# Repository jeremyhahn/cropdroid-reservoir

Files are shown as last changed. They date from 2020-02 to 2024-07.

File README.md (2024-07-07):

# cropdroid-reservoir

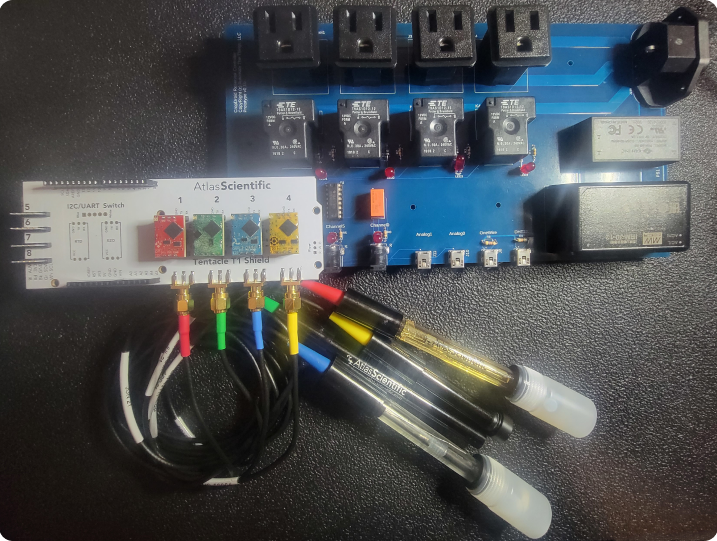
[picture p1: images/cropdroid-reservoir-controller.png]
[](https://github.com/jeremyhahn/cropdroid-reservoir)

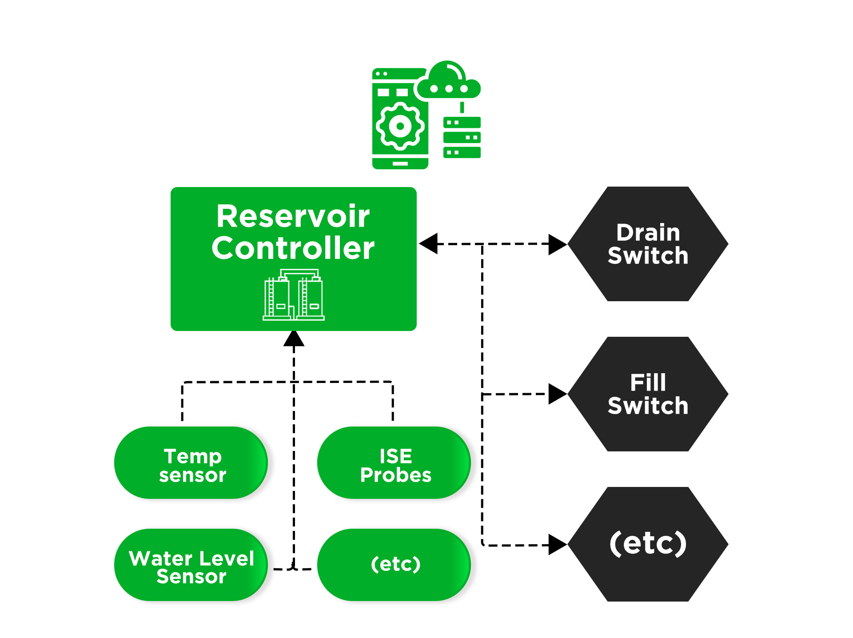
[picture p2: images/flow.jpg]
[](https://github.com/jeremyhahn/cropdroid-reservoir)

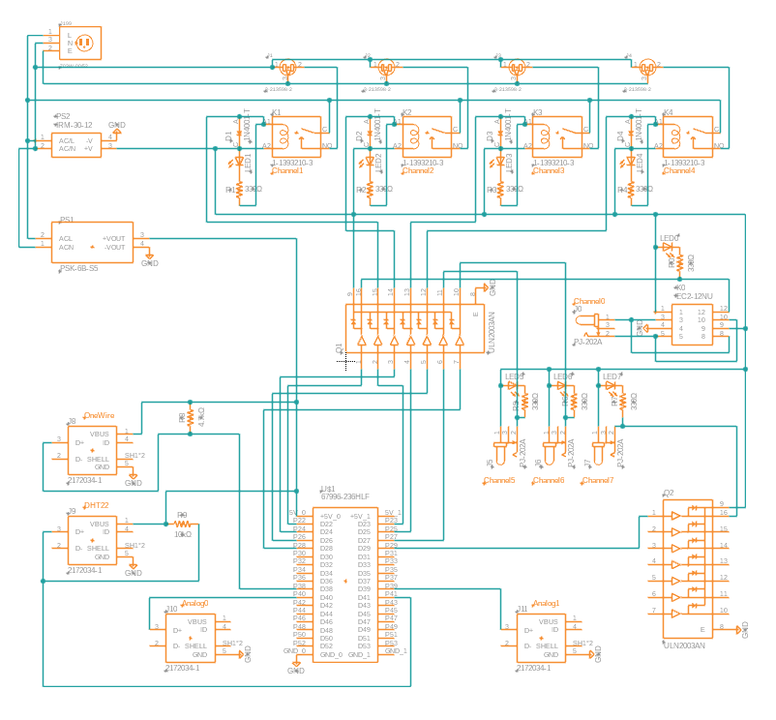
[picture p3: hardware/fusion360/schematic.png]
[](https://github.com/jeremyhahn/cropdroid-reservoir/blob/master/hardware/fusion360/schematic.png)

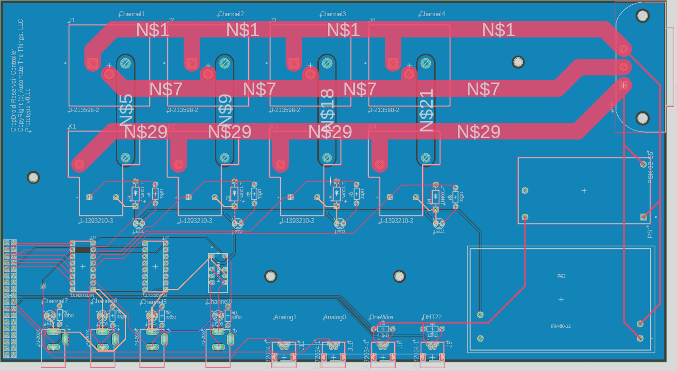
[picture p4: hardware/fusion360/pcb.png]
[](https://github.com/jeremyhahn/cropdroid-reservoir/blob/master/hardware/fusion360/pcb.png)

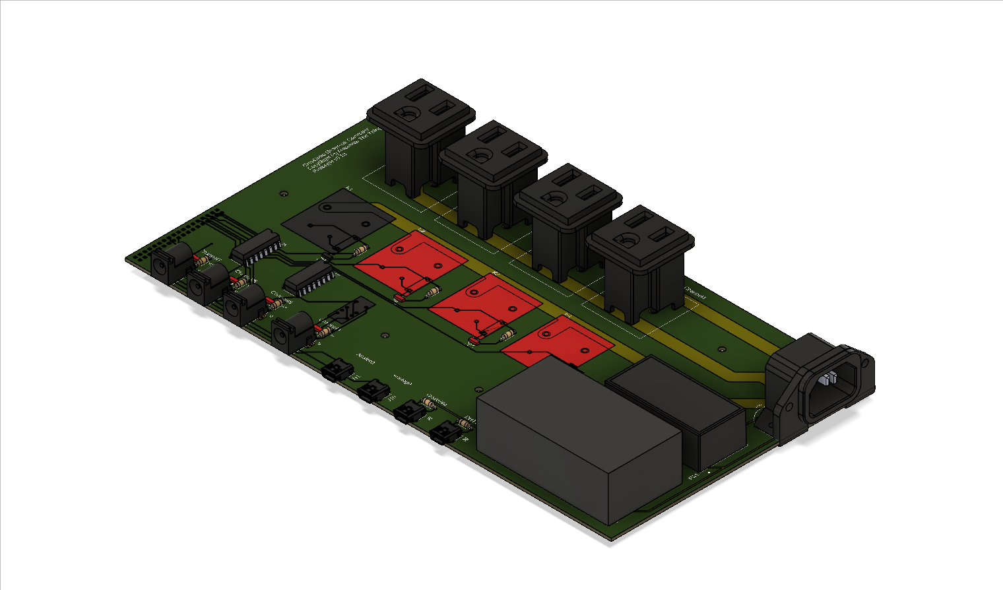
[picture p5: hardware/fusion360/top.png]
[](https://github.com/jeremyhahn/cropdroid-reservoir/blob/master/hardware/fusion360/top.png)

[](https://github.com/jeremyhahn/cropdroid-reservoir/blob/master/hardware/fusion360/top2.png)

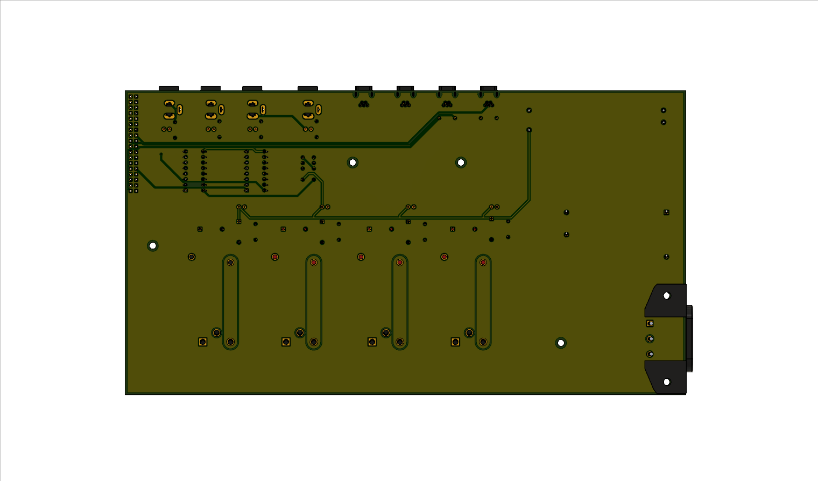
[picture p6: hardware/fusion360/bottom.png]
[](https://github.com/jeremyhahn/cropdroid-reservoir/blob/master/hardware/fusion360/bottom.png)

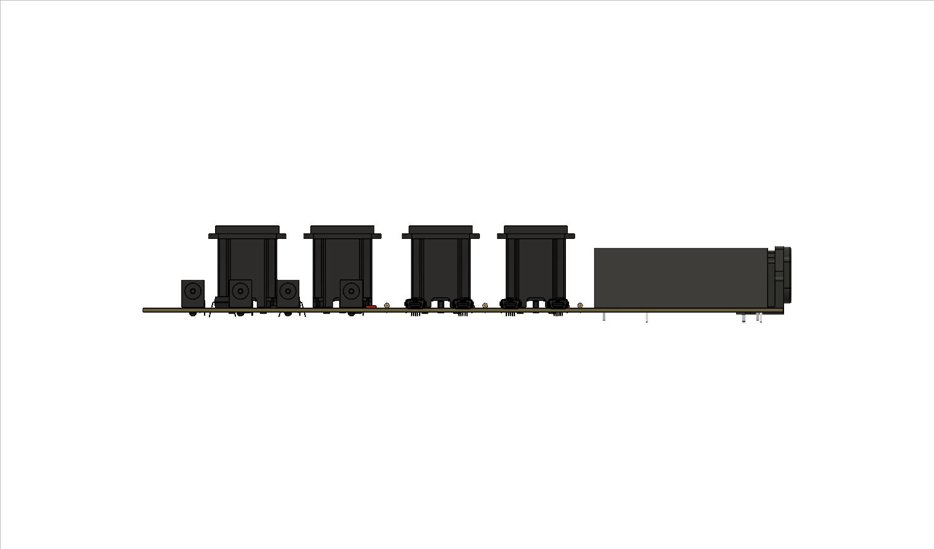
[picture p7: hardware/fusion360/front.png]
[](https://github.com/jeremyhahn/cropdroid-reservoir/blob/master/hardware/fusion360/front.png)

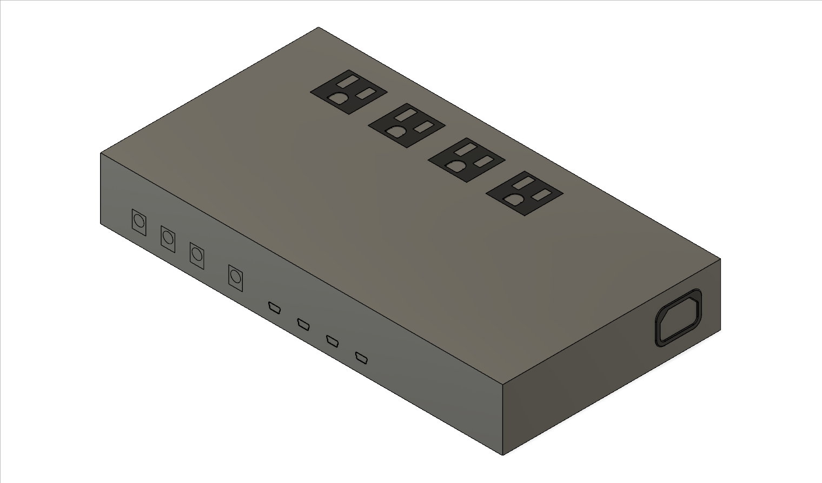
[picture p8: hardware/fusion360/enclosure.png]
[](https://github.com/jeremyhahn/cropdroid-reservoir/blob/master/hardware/fusion360/enclosure.png)

## Support

Please consider supporting this project for ongoing success and sustainability. I'm a passionate open source contributor making a professional living creating free, secure, scalable, robust, enterprise grade, distributed systems and cloud native solutions.

I'm also available for international consulting opportunities. Please let me know how I can assist you or your organization in achieving your desired security posture and technology goals.

https://github.com/sponsors/jeremyhahn

https://www.linkedin.com/in/jeremyhahn

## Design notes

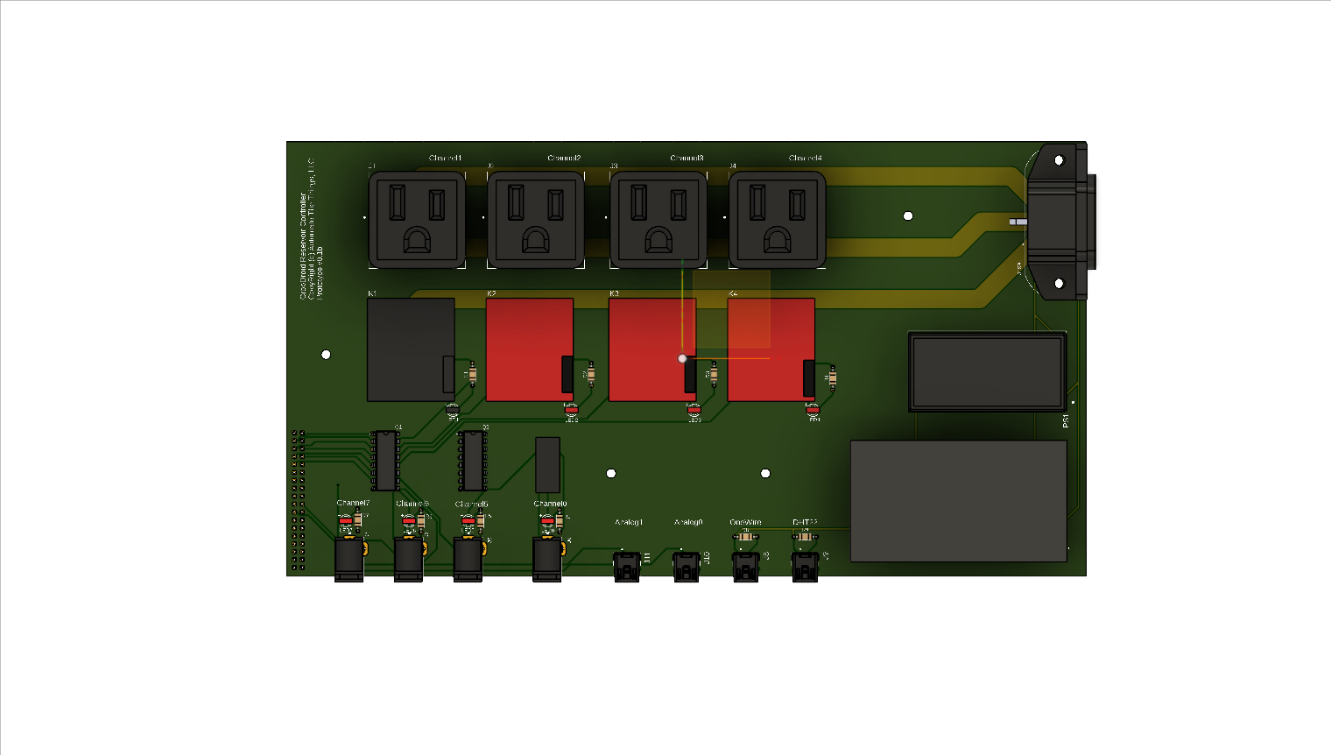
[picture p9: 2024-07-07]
hardware/fusion360/top-2.png

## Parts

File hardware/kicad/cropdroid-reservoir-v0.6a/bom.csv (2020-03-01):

Reference | Quantity | Value | Footprint | Datasheet | Category | DK_Datasheet_Link | DK_Detail_Page | Description | Digi-Key_PN | Family | MPN | Manufacturer | Status | Field4 | Field5 | Field6
D2 D4 D6 D8 | 4 | LED | libraries:CAPPRD350W60D800H2000 | ~
D3 D1 D5 D7 | 4 | 1N4001 | Diode_THT:D_DO-41_SOD81_P10.16mm_Horizontal | http://www.vishay.com/docs/88503/1n4001.pdf
J1 | 1 | 703W-00_52 | 703W-00_52:QUALTEK_703W-00_52 | B |  |  |  |  |  |  |  |  |  | Manufacturer Recommendations | Qualtek
J11 J12 J13 J14 J4 J10 | 6 | PJ-102A | digikey-footprints:Barrel_Jack_5.5mmODx2.1mmID_PJ-102A | https://www.cui.com/product/resource/digikeypdf/pj-102a.pdf | Connectors, Interconnects | https://www.cui.com/product/resource/digikeypdf/pj-102a.pdf | /product-detail/en/cui-inc/PJ-102A/CP-102A-ND/275425 | CONN PWR JACK 2X5.5MM SOLDER | CP-102A-ND | Barrel - Power Connectors | PJ-102A | CUI Inc. | Active
J3 J2 | 2 | 2172034-1 | TE_2172034-1 | Compliant |  |  |  |  |  |  |  |  |  | 2172034-1 | https://www.te.com/usa-en/product-2172034-1.html?te_bu=Cor&te_type=disp&elqCampaignId=32493
J6 J8 J5 J9 | 4 | 3-213598-2 | 3-213598-2:TE_3-213598-2 | https://www.te.com/usa-en/product-3-213598-2.html?te_bu=Cor&te_type=disp&elqCampaignId=32493 |  |  |  |  |  |  |  |  |  | Compliant | 3-213598-2 | Convenience Outlet
J7 | 1 | SAMTEC-MTSW-118-10-X-D-640 | SAMTEC-MTSW-118-10-X-D-640:SAMTEC-MTSW-118-10-X-D-640
K1 K2 K3 K4 | 4 | T9AS1D12-15 | T9AS1D12-15:RELAY_T9AS1D12-15 | https://www.te.com/usa-en/product-1-1393210-4.html?te_bu=Cor&te_type=disp&elqCampaignId=32493 |  |  |  |  |  |  |  |  |  | 1-1393210-4
PS1 | 1 | PSK-6B-S5 | PSK-6B-S5:CONV_PSK-6B-S5 | CUI Inc |  |  |  |  |  |  |  |  |  | Manufacturer recommendations | 1.0
Q1 Q2 | 2 | ULN2003AN | digikey-footprints:DIP-16_W7.62mm | http://www.ti.com/general/docs/suppproductinfo.tsp?distId=10 | Discrete Semiconductor Products | http://www.ti.com/general/docs/suppproductinfo.tsp?distId=10 | /product-detail/en/texas-instruments/ULN2003AN/296-1979-5-ND/277624 | IC PWR RELAY 7NPN 1:1 16DIP | 296-1979-5-ND | Transistors - Bipolar (BJT) - Arrays | ULN2003AN | Texas Instruments | Active
R1 | 1 | 10k | Resistor_THT:R_Axial_DIN0207_L6.3mm_D2.5mm_P10.16mm_Horizontal | ~
R2 | 1 | 4.7k | Resistor_THT:R_Axial_DIN0207_L6.3mm_D2.5mm_P10.16mm_Horizontal | ~
R3 R4 R5 R6 | 4 | R | Resistor_THT:R_Axial_DIN0207_L6.3mm_D2.5mm_P10.16mm_Horizontal | ~
RLY1 | 1 | EC2-12NU | digikey-footprints:Relay_THT_EC2 | https://api.kemet.com/component-edge/download/datasheet/EC2-12NU.pdf | Relays | https://api.kemet.com/component-edge/download/datasheet/EC2-12NU.pdf | /product-detail/en/kemet/EC2-12NU/399-11029-5-ND/4291095 | RELAY GEN PURPOSE DPDT 2A 12VDC | 399-11029-5-ND | Signal Relays, Up to 2 Amps | EC2-12NU | KEMET | Active
U1 | 1 | IRM-30-12 | IRM-30-12:IRM-30-12

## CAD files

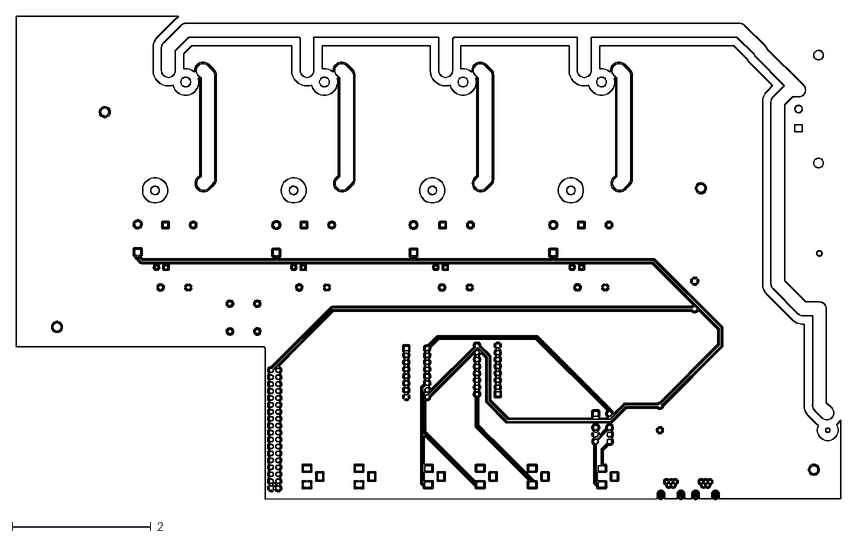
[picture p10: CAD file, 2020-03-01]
hardware/kicad/cropdroid-reservoir-v0.6a/gerber/cropdroid-reservoir-v0.6a-dxf/cropdroid-reservoir-B_Cu.dxf
11.9 x 6.97

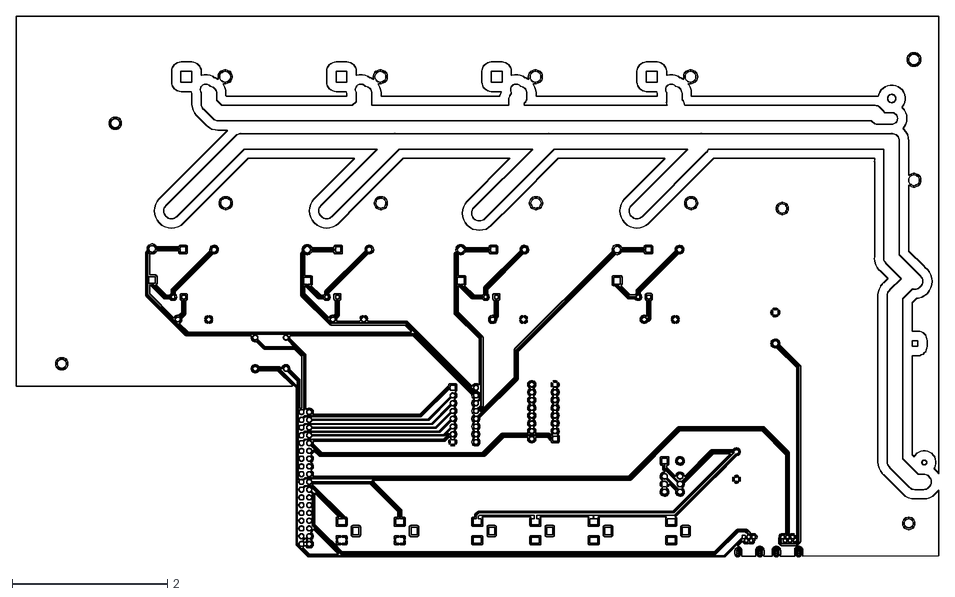
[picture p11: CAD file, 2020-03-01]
hardware/kicad/cropdroid-reservoir-v0.6a/gerber/cropdroid-reservoir-v0.6a-dxf/cropdroid-reservoir-F_Cu.dxf
11.9 x 6.97

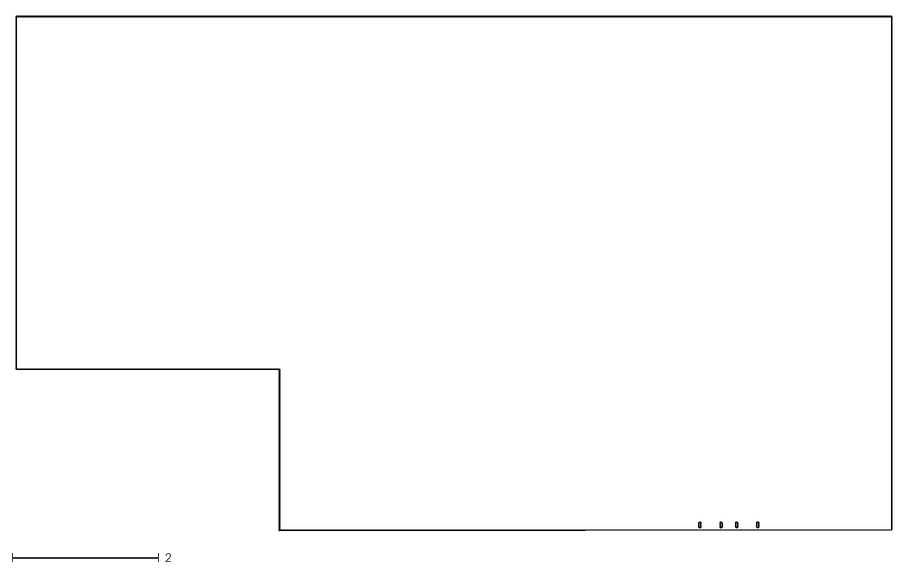
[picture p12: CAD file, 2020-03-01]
hardware/kicad/cropdroid-reservoir-v0.6a/gerber/cropdroid-reservoir-v0.6a-dxf/cropdroid-reservoir-Edge_Cuts.dxf
11.9 x 7.01

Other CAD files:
hardware/kicad/cropdroid-reservoir-v0.6a/gerber/cropdroid-reservoir-v0.6a-dxf/cropdroid-reservoir-B_Mask.dxf
hardware/kicad/cropdroid-reservoir-v0.6a/gerber/cropdroid-reservoir-v0.6a-dxf/cropdroid-reservoir-B_Paste.dxf
hardware/kicad/cropdroid-reservoir-v0.6a/gerber/cropdroid-reservoir-v0.6a-dxf/cropdroid-reservoir-F_Mask.dxf
hardware/kicad/cropdroid-reservoir-v0.6a/gerber/cropdroid-reservoir-v0.6a-dxf/cropdroid-reservoir-F_Paste.dxf
hardware/kicad/cropdroid-reservoir-v0.6a/gerber/cropdroid-reservoir-v0.6a-dxf/cropdroid-reservoir-F_SilkS.dxf

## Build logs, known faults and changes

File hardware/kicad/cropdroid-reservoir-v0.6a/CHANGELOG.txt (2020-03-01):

v0.5a
- Swap wires between pins 1 and 2 (channel 4, 5, 6)
- Change board height to accomodate vertical facing receptacles

v0.6a
- Fix upside down IRM-30-12 footprint
- Flip LED footprints
- Replace audio jacks with dc power and usb jacks
- Shorten board length

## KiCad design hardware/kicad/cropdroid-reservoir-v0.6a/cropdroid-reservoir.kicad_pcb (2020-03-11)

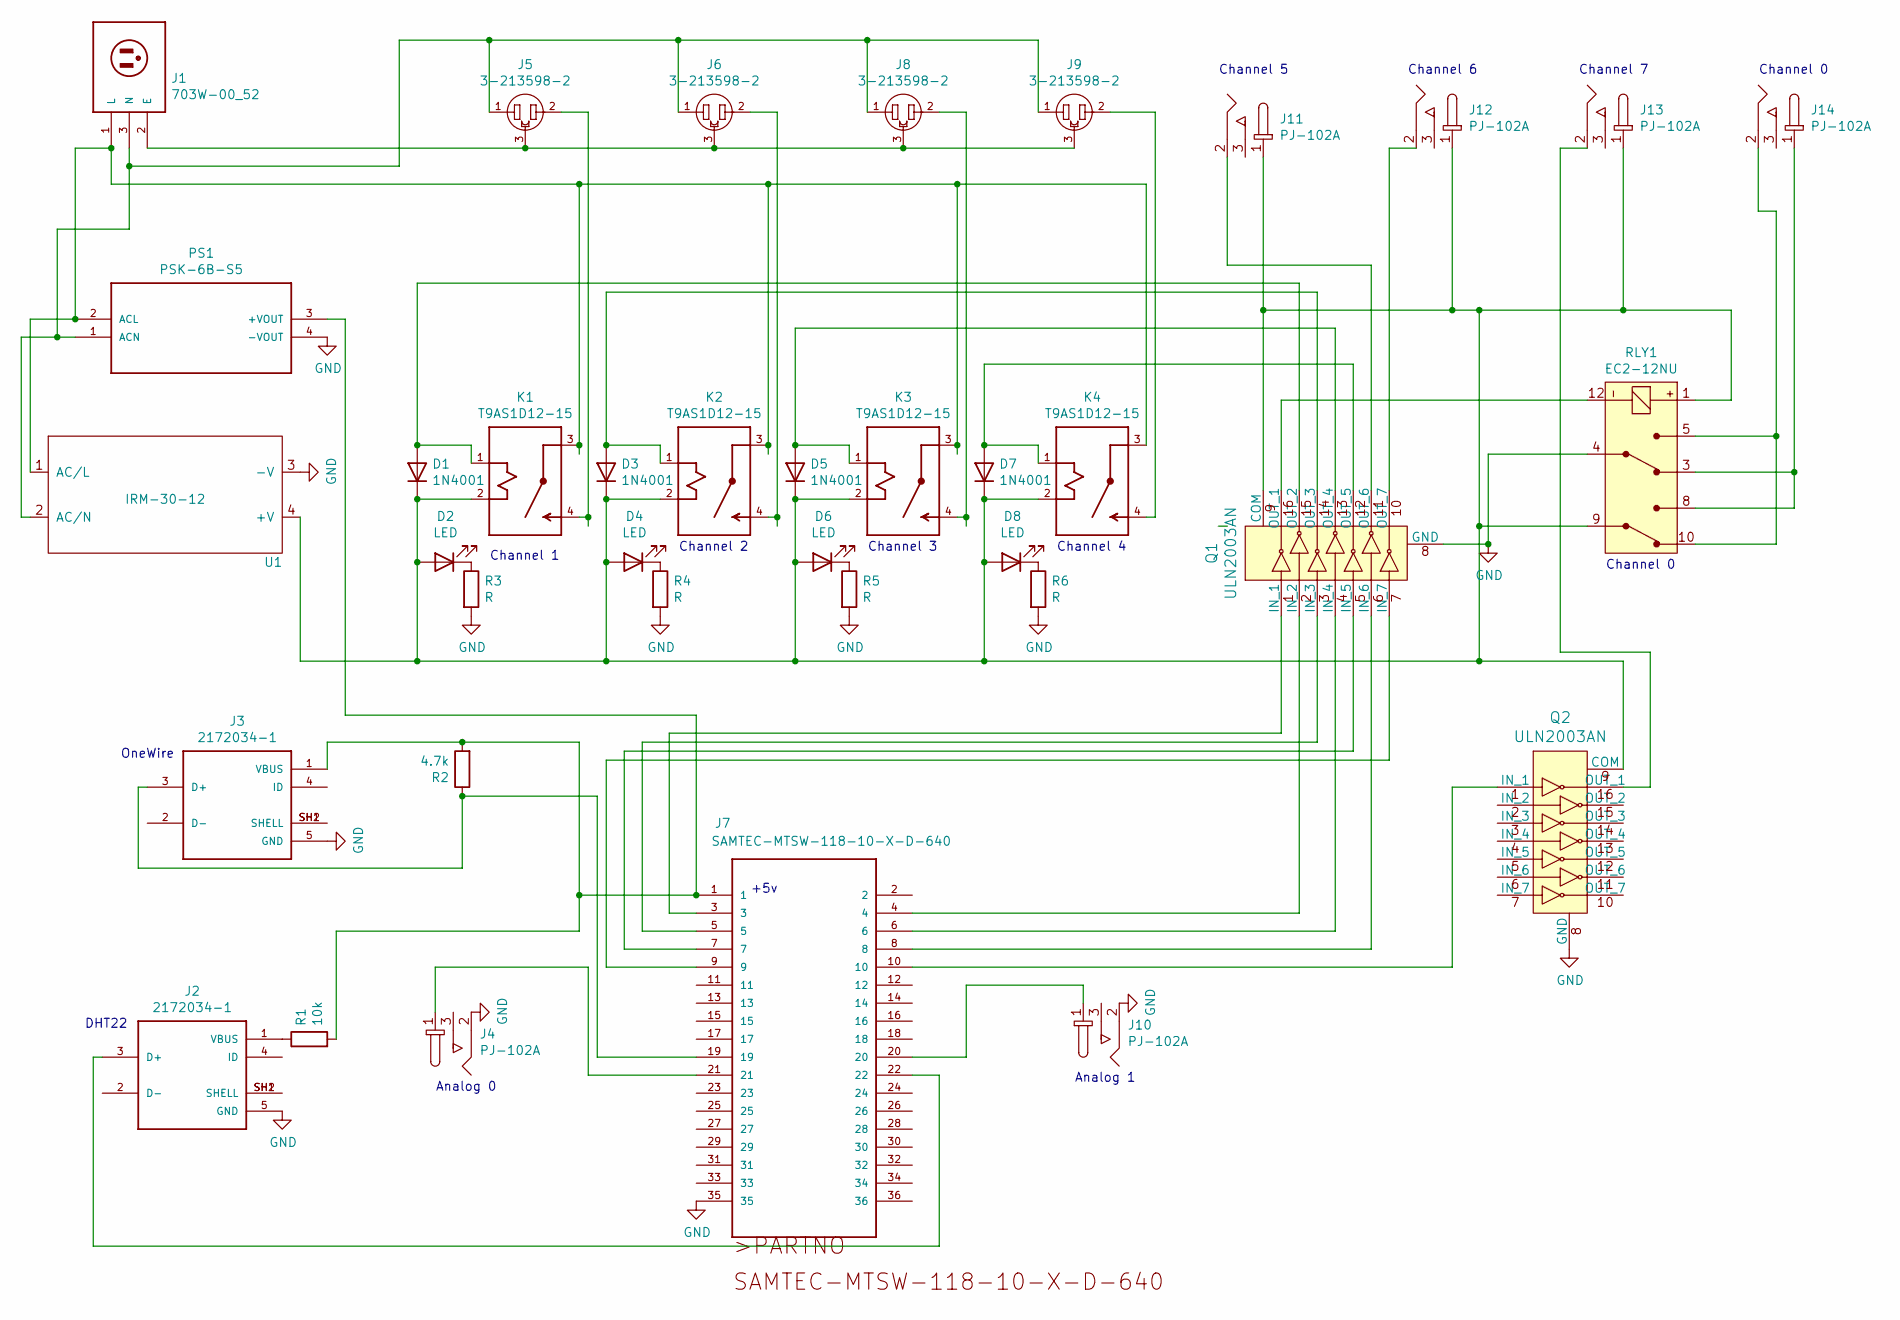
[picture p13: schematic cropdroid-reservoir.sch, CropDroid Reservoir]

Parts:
D1, D3, D5, D7: 1N4001; D_DO-41_SOD81_P10.16mm_Horizontal
D2, D4, D6, D8: LED; CAPPRD350W60D800H2000
J1: 703W-00_52; QUALTEK_703W-00_52
J2, J3: 2172034-1; TE_2172034-1
J4, J10, J11, J12, J13, J14: PJ-102A; Barrel_Jack_5.5mmODx2.1mmID_PJ-102A; MPN PJ-102A; Digi-Key_PN CP-102A-ND
J5, J6, J8, J9: 3-213598-2; TE_3-213598-2
J7: SAMTEC-MTSW-118-10-X-D-640
K1, K2, K3, K4: T9AS1D12-15; RELAY_T9AS1D12-15
PS1: PSK-6B-S5; CONV_PSK-6B-S5
Q1, Q2: ULN2003AN; DIP-16_W7.62mm; MPN ULN2003AN; Digi-Key_PN 296-1979-5-ND
R1: 10k; R_Axial_DIN0207_L6.3mm_D2.5mm_P10.16mm_Horizontal
R2: 4.7k; R_Axial_DIN0207_L6.3mm_D2.5mm_P10.16mm_Horizontal
R3, R4, R5, R6: R; R_Axial_DIN0207_L6.3mm_D2.5mm_P10.16mm_Horizontal
RLY1: EC2-12NU; Relay_THT_EC2; MPN EC2-12NU; Digi-Key_PN 399-11029-5-ND
U1: IRM-30-12

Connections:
GND: J2.5 (GND), J3.5 (GND), J4.2, J7.35, J10.2, PS1.4 (-VOUT), Q1.8 (GND), Q2.8 (GND), R3.2, R4.2, R5.2, R6.2, RLY1.4 (COM1), U1.3 (-V)
unnamed: D1.1 (K), D2.2 (A), D3.1 (K), D4.2 (A), D5.1 (K), D6.2 (A), D7.1 (K), D8.2 (A), J11.1, J12.1, J13.1, K1.2 (A2), K2.2 (A2), K3.2 (A2), K4.2 (A2), Q1.9 (COM), Q2.9 (COM), RLY1.1 (COIL), RLY1.9 (COM2), U1.4 (+V)
unnamed: D1.2 (A), K1.1 (A1), Q1.15 (OUT_2)
unnamed: D2.1 (K), R3.1
unnamed: D3.2 (A), K2.1 (A1), Q1.14 (OUT_3)
unnamed: D4.1 (K), R4.1
unnamed: D5.2 (A), K3.1 (A1), Q1.13 (OUT_4)
unnamed: D6.1 (K), R5.1
unnamed: D7.2 (A), K4.1 (A1), Q1.12 (OUT_5)
unnamed: D8.1 (K), R6.1
unnamed: J1.1 (L), K1.3 (C), K2.3 (C), K3.3 (C), K4.3 (C), PS1.2 (ACL), U1.1 (AC/L)
unnamed: J1.2 (E), J5.3, J6.3, J8.3, J9.3
unnamed: J1.3 (N), J5.1, J6.1, J8.1, J9.1, PS1.1 (ACN), U1.2 (AC/N)
unnamed: J2.1 (VBUS), R1.1
unnamed: J2.3 (D+), J7.22
unnamed: J2.SH1 (SHELL), J2.SH2 (SHELL)
unnamed: J3.1 (VBUS), J7.1, PS1.3 (+VOUT), R1.2, R2.2
unnamed: J3.3 (D+), J7.19, R2.1
unnamed: J3.SH1 (SHELL), J3.SH2 (SHELL)
unnamed: J4.1, J7.21
unnamed: J5.2, K1.4 (NO)
unnamed: J6.2, K2.4 (NO)
unnamed: J7.3, Q1.1 (IN_1)
unnamed: J7.4, Q1.2 (IN_2)
unnamed: J7.5, Q1.3 (IN_3)
unnamed: J7.6, Q1.4 (IN_4)
unnamed: J7.7, Q1.5 (IN_5)
unnamed: J7.8, Q1.6 (IN_6)
unnamed: J7.9, Q1.7 (IN_7)
unnamed: J7.10, Q2.1 (IN_1)
unnamed: J8.2, K3.4 (NO)
unnamed: J9.2, K4.4 (NO)
unnamed: J7.20, J10.1
unnamed: J11.2, Q1.11 (OUT_6)
unnamed: J12.2, Q1.10 (OUT_7)
unnamed: J13.2, Q2.16 (OUT_1)
unnamed: J14.1, RLY1.3 (NC1), RLY1.8 (NO2)
unnamed: J14.2, RLY1.5 (NO1), RLY1.10 (NC2)
unnamed: Q1.16 (OUT_1), RLY1.12 (COIL)

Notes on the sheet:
Channel 1
Channel 2
Channel 3
Channel 0
Channel 5
Channel 6
Channel 7
Analog 0
Analog 1
DHT22
+5v
Channel 4
OneWire

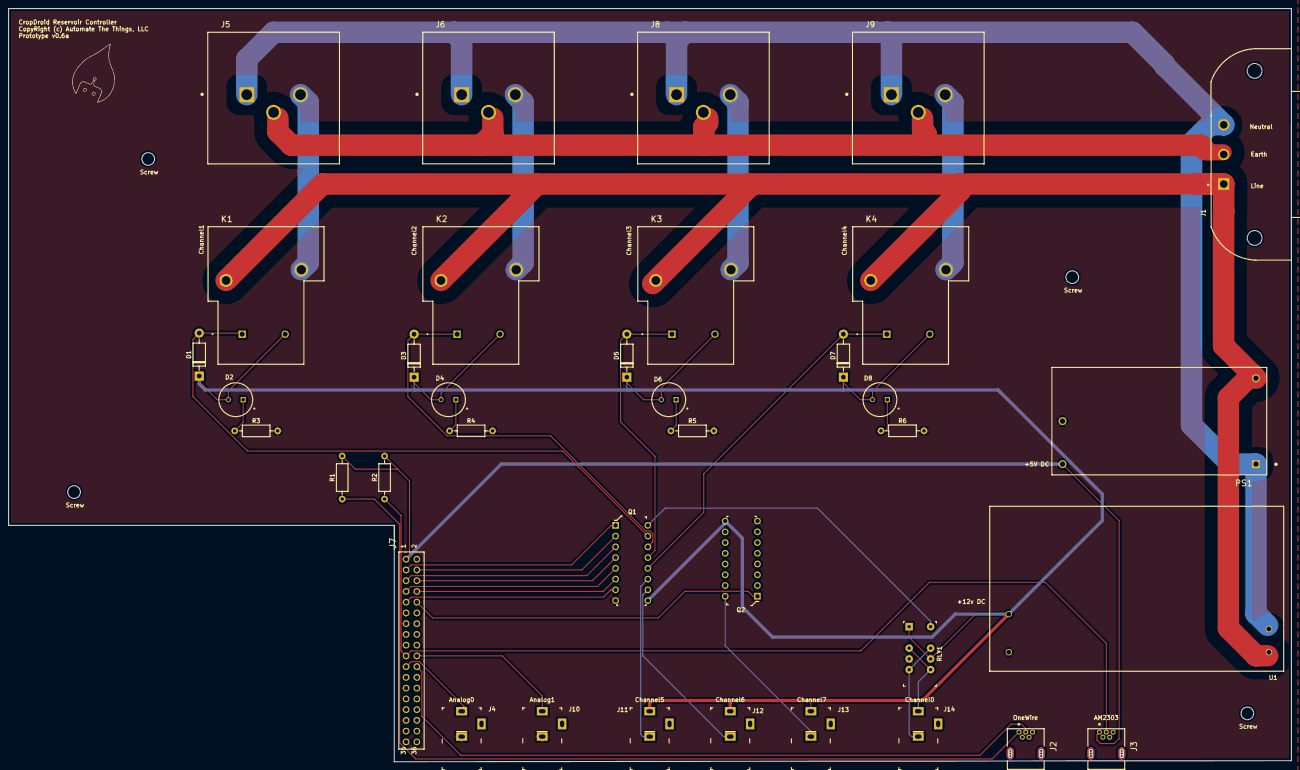
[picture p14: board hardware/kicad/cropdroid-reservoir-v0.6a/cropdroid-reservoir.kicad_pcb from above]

Board: 2 copper layers, 303.3 x 178.1 mm, 41 parts (0 on the bottom side), 39 nets.

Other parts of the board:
Screw: Drill; Drill_Hole
Screw#2, Screw#3, Screw#4: Drill; Drill_Hole

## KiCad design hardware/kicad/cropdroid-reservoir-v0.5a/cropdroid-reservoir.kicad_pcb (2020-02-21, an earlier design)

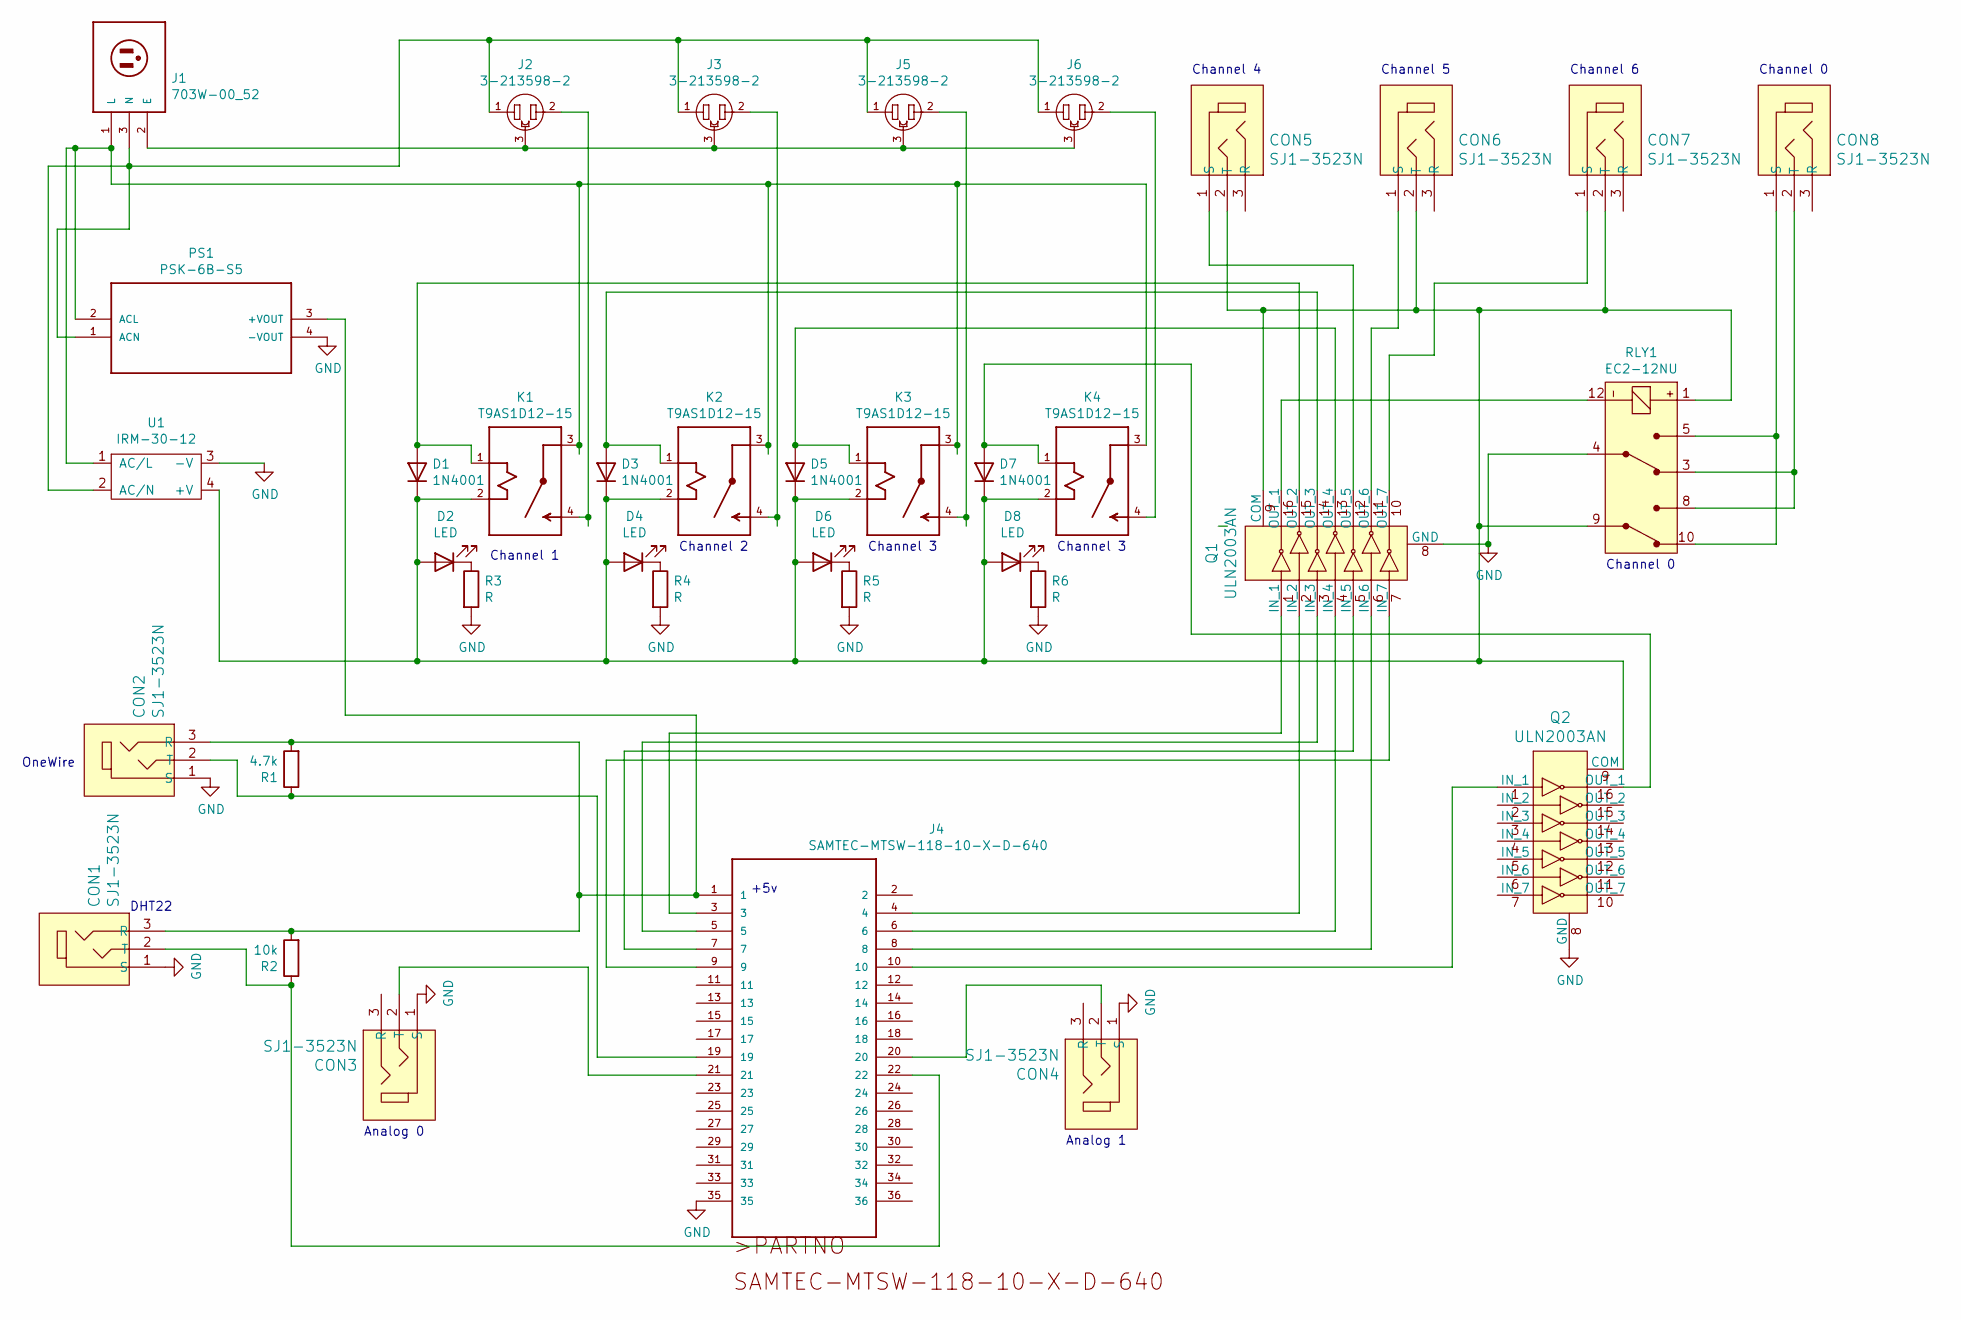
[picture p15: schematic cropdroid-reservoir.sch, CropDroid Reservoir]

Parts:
CON1, CON2, CON3, CON4, CON5, CON6, CON7, CON8: SJ1-3523N; Headphone_Jack_3.5mm_SJ1-3523N; MPN SJ1-3523N; Digi-Key_PN CP1-3523N-ND
D1, D3, D5, D7: 1N4001; D_DO-41_SOD81_P10.16mm_Horizontal
D2, D4, D6, D8: LED; CAPPRD350W60D800H2000
J1: 703W-00_52; QUALTEK_703W-00_52
J2, J3, J5, J6: 3-213598-2; TE_3-213598-2
J4: SAMTEC-MTSW-118-10-X-D-640
K1, K2, K3, K4: T9AS1D12-15; RELAY_T9AS1D12-15
PS1: PSK-6B-S5; CONV_PSK-6B-S5
Q1, Q2: ULN2003AN; DIP-16_W7.62mm; MPN ULN2003AN; Digi-Key_PN 296-1979-5-ND
R1: 4.7k; R_Axial_DIN0207_L6.3mm_D2.5mm_P10.16mm_Horizontal
R2: 10k; R_Axial_DIN0207_L6.3mm_D2.5mm_P10.16mm_Horizontal
R3, R4, R5, R6: R; R_Axial_DIN0207_L6.3mm_D2.5mm_P10.16mm_Horizontal
RLY1: EC2-12NU; Relay_THT_EC2; MPN EC2-12NU; Digi-Key_PN 399-11029-5-ND
U1: IRM-30-12

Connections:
GND: CON1.1 (S), CON2.1 (S), CON3.1 (S), CON4.1 (S), J4.35, PS1.4 (-VOUT), Q1.8 (GND), Q2.8 (GND), R3.2, R4.2, R5.2, R6.2, RLY1.4 (COM1), U1.3 (-V)
unnamed: CON1.2 (T), J4.22, R2.1
unnamed: CON1.3 (R), CON2.3 (R), J4.1, PS1.3 (+VOUT), R1.2, R2.2
unnamed: CON2.2 (T), J4.19, R1.1
unnamed: CON3.2 (T), J4.21
unnamed: CON4.2 (T), J4.20
unnamed: CON5.1 (S), Q1.12 (OUT_5)
unnamed: CON5.2 (T), CON6.2 (T), CON7.2 (T), D1.1 (K), D2.2 (A), D3.1 (K), D4.2 (A), D5.1 (K), D6.2 (A), D7.1 (K), D8.2 (A), K1.2 (A2), K2.2 (A2), K3.2 (A2), K4.2 (A2), Q1.9 (COM), Q2.9 (COM), RLY1.1 (COIL), RLY1.9 (COM2), U1.4 (+V)
unnamed: CON6.1 (S), Q1.11 (OUT_6)
unnamed: CON7.1 (S), Q1.10 (OUT_7)
unnamed: CON8.1 (S), RLY1.5 (NO1), RLY1.10 (NC2)
unnamed: CON8.2 (T), RLY1.3 (NC1), RLY1.8 (NO2)
unnamed: D1.2 (A), K1.1 (A1), Q1.15 (OUT_2)
unnamed: D2.1 (K), R3.1
unnamed: D3.2 (A), K2.1 (A1), Q1.14 (OUT_3)
unnamed: D4.1 (K), R4.1
unnamed: D5.2 (A), K3.1 (A1), Q1.13 (OUT_4)
unnamed: D6.1 (K), R5.1
unnamed: D7.2 (A), K4.1 (A1), Q2.16 (OUT_1)
unnamed: D8.1 (K), R6.1
unnamed: J1.1 (L), K1.3 (C), K2.3 (C), K3.3 (C), K4.3 (C), PS1.2 (ACL), U1.1 (AC/L)
unnamed: J1.2 (E), J2.3, J3.3, J5.3, J6.3
unnamed: J1.3 (N), J2.1, J3.1, J5.1, J6.1, PS1.1 (ACN), U1.2 (AC/N)
unnamed: J2.2, K1.4 (NO)
unnamed: J3.2, K2.4 (NO)
unnamed: J4.3, Q1.1 (IN_1)
unnamed: J4.4, Q1.2 (IN_2)
unnamed: J4.5, Q1.3 (IN_3)
unnamed: J4.6, Q1.4 (IN_4)
unnamed: J4.7, Q1.5 (IN_5)
unnamed: J4.8, Q1.6 (IN_6)
unnamed: J4.9, Q1.7 (IN_7)
unnamed: J4.10, Q2.1 (IN_1)
unnamed: J5.2, K3.4 (NO)
unnamed: J6.2, K4.4 (NO)
unnamed: Q1.16 (OUT_1), RLY1.12 (COIL)

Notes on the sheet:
Channel 1
Channel 2
Channel 3
Channel 0
Channel 4
Channel 5
Channel 6
Analog 0
Analog 1
OneWire
DHT22
+5v

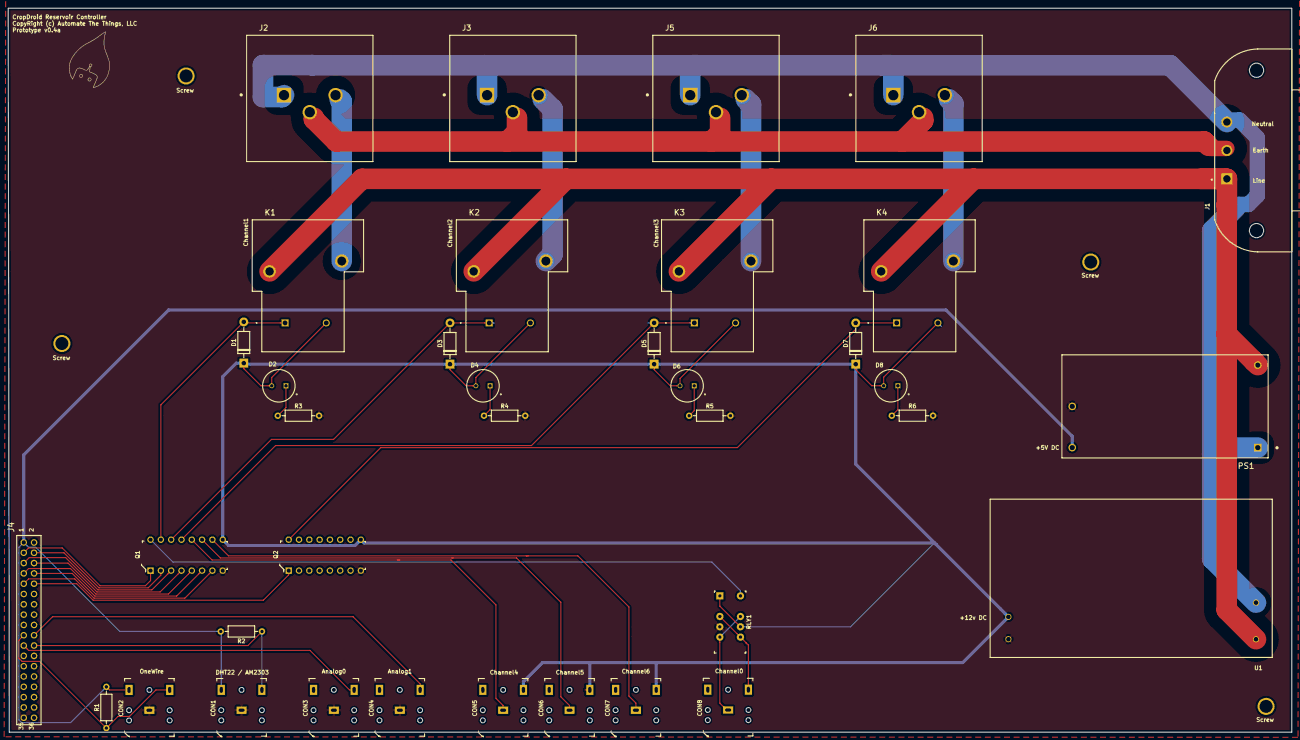
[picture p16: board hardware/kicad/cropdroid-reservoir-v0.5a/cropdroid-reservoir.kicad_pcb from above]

Board: 2 copper layers, 316.2 x 178.4 mm, 41 parts (0 on the bottom side), 36 nets.

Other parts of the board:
Screw: Drill; Drill_Hole
Screw#2, Screw#3, Screw#4: Drill; Drill_Hole

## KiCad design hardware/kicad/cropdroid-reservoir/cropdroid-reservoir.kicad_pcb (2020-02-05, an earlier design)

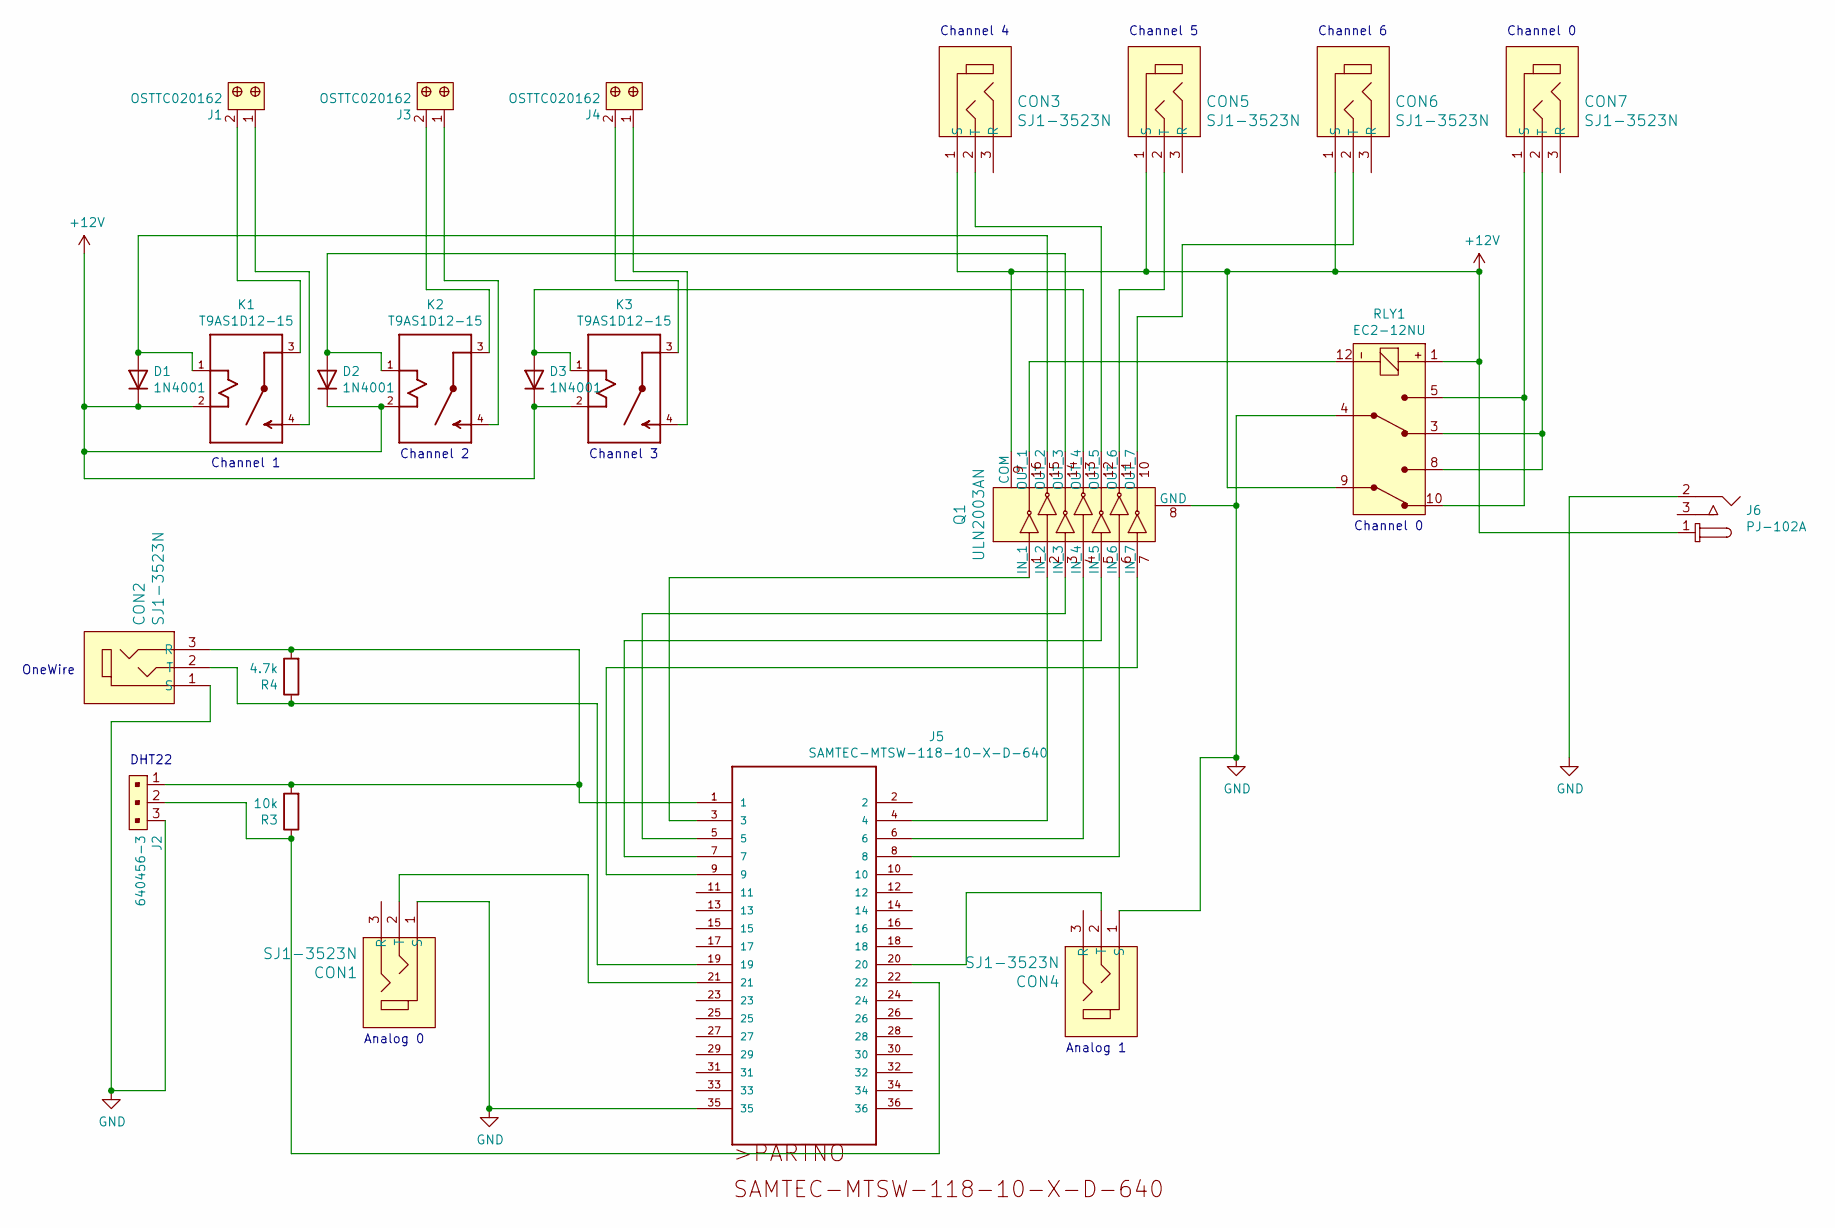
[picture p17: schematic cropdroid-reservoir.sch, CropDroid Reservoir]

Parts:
CON1, CON2, CON3, CON4, CON5, CON6, CON7: SJ1-3523N; Headphone_Jack_3.5mm_SJ1-3523N; MPN SJ1-3523N; Digi-Key_PN CP1-3523N-ND
D1, D2, D3: 1N4001; D_DO-41_SOD81_P10.16mm_Horizontal
J1, J3, J4: OSTTC020162; Term_Block_1x2_P5mm; MPN OSTTC020162; Digi-Key_PN ED2600-ND
J2: 640456-3; PinHeader_1x3_P2.54_Drill1.1mm; MPN 640456-3; Digi-Key_PN A19470-ND
J5: SAMTEC-MTSW-118-10-X-D-640
J6: PJ-102A; Barrel_Jack_5.5mmODx2.1mmID_PJ-102A; MPN PJ-102A; Digi-Key_PN CP-102A-ND
K1, K2, K3: T9AS1D12-15; RELAY_T9AS1D12-15
Q1: ULN2003AN; DIP-16_W7.62mm; MPN ULN2003AN; Digi-Key_PN 296-1979-5-ND
R3: 10k; R_Axial_DIN0207_L6.3mm_D2.5mm_P10.16mm_Horizontal
R4: 4.7k; R_Axial_DIN0207_L6.3mm_D2.5mm_P10.16mm_Horizontal
RLY1: EC2-12NU; Relay_THT_EC2; MPN EC2-12NU; Digi-Key_PN 399-11029-5-ND

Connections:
+12V: CON3.1 (S), CON5.1 (S), CON6.1 (S), D1.1 (K), D2.1 (K), D3.1 (K), J6.1, K1.2 (A2), K2.2 (A2), K3.2 (A2), Q1.9 (COM), RLY1.1 (COIL), RLY1.9 (COM2)
GND: CON1.1 (S), CON2.1 (S), CON4.1 (S), J2.3, J5.35, J6.2, Q1.8 (GND), RLY1.4 (COM1)
unnamed: CON1.2 (T), J5.21
unnamed: CON2.2 (T), J5.19, R4.1
unnamed: CON2.3 (R), J2.1, J5.1, R3.2, R4.2
unnamed: CON3.2 (T), Q1.12 (OUT_5)
unnamed: CON4.2 (T), J5.20
unnamed: CON5.2 (T), Q1.11 (OUT_6)
unnamed: CON6.2 (T), Q1.10 (OUT_7)
unnamed: CON7.1 (S), RLY1.5 (NO1), RLY1.10 (NC2)
unnamed: CON7.2 (T), RLY1.3 (NC1), RLY1.8 (NO2)
unnamed: D1.2 (A), K1.1 (A1), Q1.15 (OUT_2)
unnamed: D2.2 (A), K2.1 (A1), Q1.14 (OUT_3)
unnamed: D3.2 (A), K3.1 (A1), Q1.13 (OUT_4)
unnamed: J1.1, K1.4 (NO)
unnamed: J1.2, K1.3 (C)
unnamed: J2.2, J5.22, R3.1
unnamed: J3.1, K2.4 (NO)
unnamed: J3.2, K2.3 (C)
unnamed: J4.1, K3.4 (NO)
unnamed: J4.2, K3.3 (C)
unnamed: J5.3, Q1.1 (IN_1)
unnamed: J5.4, Q1.2 (IN_2)
unnamed: J5.5, Q1.3 (IN_3)
unnamed: J5.6, Q1.4 (IN_4)
unnamed: J5.7, Q1.5 (IN_5)
unnamed: J5.8, Q1.6 (IN_6)
unnamed: J5.9, Q1.7 (IN_7)
unnamed: Q1.16 (OUT_1), RLY1.12 (COIL)

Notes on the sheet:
Channel 1
Channel 2
Channel 3
Channel 0
Channel 4
Channel 5
Channel 6
Analog 0
Analog 1
OneWire
DHT22

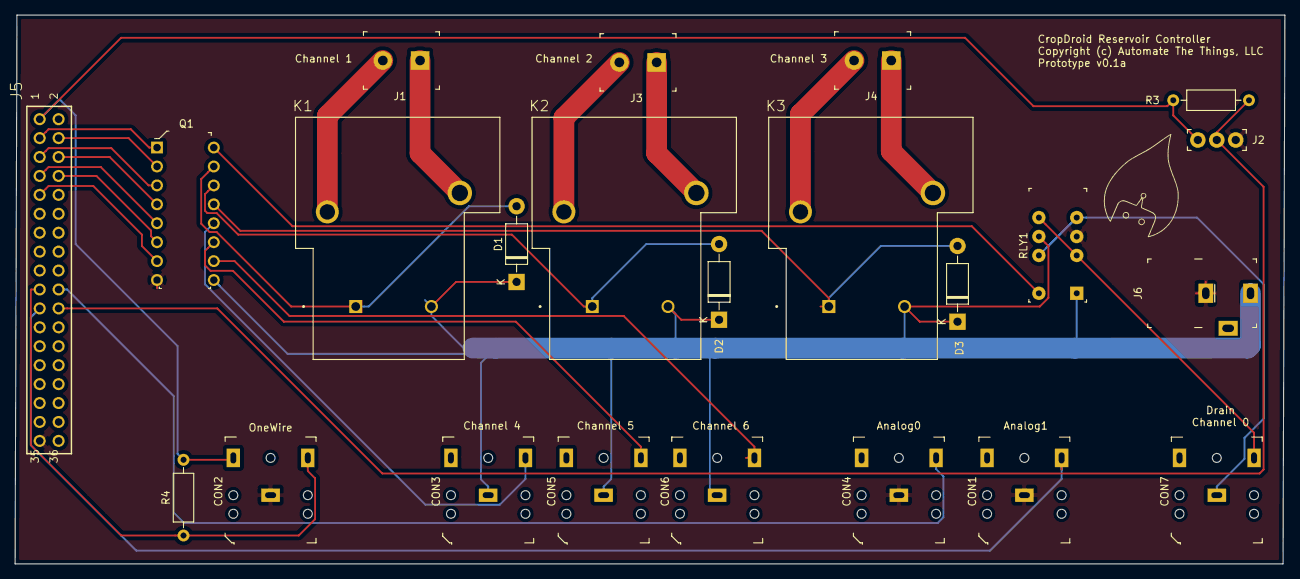
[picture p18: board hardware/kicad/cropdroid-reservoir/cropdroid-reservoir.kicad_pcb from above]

Board: 2 copper layers, 170.4 x 73.7 mm, 23 parts (0 on the bottom side), 29 nets.

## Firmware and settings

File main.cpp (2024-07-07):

// SPDX-License-Identifier: AGPL-3.0-or-later
// SPDX-License-Identifier: commercial

#include <Arduino.h>
#include <SPI.h>
#include "Ethernet.h"
#include "DHT.h"
#include <Wire.h>
#include "OneWire.h"
#include "DallasTemperature.h"
#include "EEPROM.h"

#define DEBUG 1
#define EEPROM_DEBUG 1
#define BUFSIZE 255
#define CHANNEL_SIZE 16

#define ONE_WIRE_BUS 38
#define DHT_ENV_PIN  41
//#define UPPER_FLOAT A0
//#define LOWER_FLOAT A1

#define UPPER_FLOAT A14
#define LOWER_FLOAT A15

extern int  __bss_end;
extern int  *__brkval;

const char json_bracket_open[] = "{";
const char json_bracket_close[] = "}";
const char json_array_bracket_close[] = "]";
const char json_comma[] = ",";

const char string_initializing[] PROGMEM = "Initializing reservoir...";
const char string_dhcp_failed[] PROGMEM = "DHCP Failed";
const char string_http_200[] PROGMEM = "HTTP/1.1 200 OK";
const char string_http_404[] PROGMEM = "HTTP/1.1 404 Not Found";
const char string_http_500[] PROGMEM = "HTTP/1.1 500 Internal Server Error";
const char string_http_content_type_json[] PROGMEM = "Content-Type: application/json";
const char string_http_xpowered_by[] PROGMEM = "X-Powered-By: CropDroid";
const char string_rest_address[] PROGMEM = "REST service listening on: ";
const char string_switch_on[] PROGMEM = "Switching on";
const char string_switch_off[] PROGMEM = "Switching off";
const char string_json_key_metrics[] PROGMEM = "\"metrics\":{";
const char string_json_key_mem[] PROGMEM = "\"mem\":";
const char string_json_key_envTemp[] PROGMEM = ",\"envTemp\":";
const char string_json_key_envHumidity[] PROGMEM = ",\"envHumidity\":";
const char string_json_key_envHeatIndex[] PROGMEM = ",\"envHeatIndex\":";
const char string_json_key_ph[] PROGMEM = ",\"ph\":";
const char string_json_key_ec[] PROGMEM = ",\"ec\":";
const char string_json_key_tds[] PROGMEM = ",\"tds\":";
const char string_json_key_sal[] PROGMEM = ",\"sal\":";
const char string_json_key_sg[] PROGMEM = ",\"sg\":";
const char string_json_key_do_mgl[] PROGMEM = ",\"do_mgL\":";
const char string_json_key_do_per[] PROGMEM = ",\"do_per\":";
const char string_json_key_orp[] PROGMEM = ",\"orp\":";
const char string_json_key_resTemp[] PROGMEM = ",\"resTemp\":";
const char string_json_key_upperFloat[] PROGMEM = ",\"upperFloat\":";
const char string_json_key_lowerFloat[] PROGMEM = ",\"lowerFloat\":";
const char string_json_key_channels[] PROGMEM = ",\"channels\":[";
const char string_json_key_channel[] PROGMEM = "\"channel\":";
const char string_json_key_pin[] PROGMEM = ",\"pin\":";
const char string_json_key_position[] PROGMEM =  ",\"position\":";
const char string_json_key_value[] PROGMEM =  ",\"value\":";
const char string_json_key_address[] PROGMEM =  "\"address\":";
const char string_json_bracket_open[] PROGMEM = "{";
const char string_json_bracket_close[] PROGMEM = "}";
const char string_json_error_invalid_channel[] PROGMEM = "\"error\":\"Invalid channel\"";
const char string_json_reboot_true PROGMEM = "\"reboot\":true";
const char string_json_reset_true PROGMEM = "\"reset\":true";
const char string_hardware_version[] PROGMEM = "\"hardware\":\"res-v0.1b\",";
const char string_firmware_version[] PROGMEM = "\"firmware\":\"1.0.0b\"";
const char string_json_key_uptime[] PROGMEM = ",\"uptime\":";
const char * const string_table[] PROGMEM = {
  string_initializing,
  string_dhcp_failed,
  string_http_200,
  string_http_404,
  string_http_500,
  string_http_content_type_json,
  string_http_xpowered_by,
  string_rest_address,
  string_switch_on,
  string_switch_off,
  string_json_key_metrics,
  string_json_key_mem,
  string_json_key_envTemp,
  string_json_key_envHumidity,
  string_json_key_envHeatIndex,
  string_json_key_ph,
  string_json_key_ec,
  string_json_key_tds,
  string_json_key_sal,
  string_json_key_sg,
  string_json_key_do_mgl,
  string_json_key_do_per,
  string_json_key_orp,
  string_json_key_resTemp,
  string_json_key_upperFloat,
  string_json_key_lowerFloat,
  string_json_key_channels,
  string_json_key_channel,
  string_json_key_pin,
  string_json_key_position,
  string_json_key_value,
  string_json_key_address,
  string_json_bracket_open,
  string_json_bracket_close,
  string_json_error_invalid_channel,
  string_json_reboot_true,
  string_json_reset_true,
  string_hardware_version,
  string_firmware_version,
  string_json_key_uptime
};
int idx_initializing = 0,
    idx_dhcp_failed = 1,
	idx_http_200 = 2,
	idx_http_404 = 3,
	idx_http_500 = 4,
	idx_http_content_type_json = 5,
	idx_http_xpowered_by = 6,
	idx_rest_address = 7,
	idx_switch_on = 8,
	idx_switch_off = 9,
	idx_json_key_metrics = 10,
	idx_json_key_mem = 11,
	idx_json_key_envTemp = 12,
	idx_json_key_envHumidity = 13,
	idx_json_key_envHeatIndex = 14,
	idx_json_key_ph = 15,
	idx_json_key_ec = 16,
	idx_json_key_tds = 17,
	idx_json_key_sal = 18,
	idx_json_key_sg = 19,
	idx_json_key_do_mgl = 20,
	idx_json_key_do_per = 21,
	idx_json_key_orp = 22,
	idx_json_key_resTemp = 23,
	idx_json_key_upperFloat = 24,
	idx_json_key_lowerFloat = 25,
	idx_json_key_channels = 26,
	idx_json_key_channel = 27,
	idx_json_key_pin = 28,
	idx_json_key_position = 29,
	idx_json_key_value = 30,
	idx_json_key_address = 31,
	idx_json_key_bracket_open = 32,
	idx_json_key_bracket_close = 33,
	idx_json_error_invalid_channel = 34,
	idx_json_reboot_true = 35,
	idx_json_reset_true = 36,
	idx_hardware_version = 37,
	idx_firmware_version = 38,
	idx_json_key_uptime = 39;
char string_buffer[60];
char float_buffer[10];

const int NULL_CHANNEL = 255;
const uint8_t channels[CHANNEL_SIZE] = {
	22, 23, 24, 25, 26, 27, 28, 29,
	30, 31, 32, 33, 34, 35, 36, 37
};
unsigned long channel_table[CHANNEL_SIZE][3] = {
	// channel, start, interval
   {NULL_CHANNEL, 0, 0},
   {NULL_CHANNEL, 0, 0},
   {NULL_CHANNEL, 0, 0},
   {NULL_CHANNEL, 0, 0},
   {NULL_CHANNEL, 0, 0},
   {NULL_CHANNEL, 0, 0},
   {NULL_CHANNEL, 0, 0},
   {NULL_CHANNEL, 0, 0},
   {NULL_CHANNEL, 0, 0},
   {NULL_CHANNEL, 0, 0},
   {NULL_CHANNEL, 0, 0},
   {NULL_CHANNEL, 0, 0},
   {NULL_CHANNEL, 0, 0},
   {NULL_CHANNEL, 0, 0},
   {NULL_CHANNEL, 0, 0},
   {NULL_CHANNEL, 0, 0}
};

DHT envDHT(DHT_ENV_PIN, DHT22);
OneWire oneWire(ONE_WIRE_BUS);
DallasTemperature sensors(&oneWire);

float envTemp, envHumidity, envHeatIndex,
      PH, EC, TDS, SAL, SG, DO_mgL, DO_PER, ORP = 0.0,
	  pod0Temp, pod1Temp, resTemp;

int EC_ID = 100, PH_ID = 99, DO_ID = 97, ORP_ID = 98, systemTemp = 0;

void readProbe(int channel, float *probe);
void readTempHumidity();
void readResTemp();
void debug(String msg);
void switchOn(int pin);
void switchOff(int pin);
void handleActiveChannels();
void handleWebRequest();
void send404();
void resetDefaults();
int availableMemory();
void(* resetFunc) (void) = 0;

byte defaultMac[] = { 0x04, 0x02, 0x00, 0x00, 0x00, 0x02 };

byte mac[] = {
	EEPROM.read(0),
	EEPROM.read(1),
	EEPROM.read(2),
	EEPROM.read(3),
	EEPROM.read(4),
	EEPROM.read(5)
};
IPAddress ip(
  EEPROM.read(6),
  EEPROM.read(7),
  EEPROM.read(8),
  EEPROM.read(9));

EthernetServer httpServer(80);
EthernetClient httpClient;

int main(void) {
  init();
  setup();

  for (;;)
    loop();

  return 0;
}

void setup(void) {

  //EEPROM.write(0, 255);

  Wire.begin();
  envDHT.begin();
  sensors.begin();

  analogReference(DEFAULT);

  for(int i=0; i<CHANNEL_SIZE; i++) {
    pinMode(channels[i], OUTPUT);
    digitalWrite(channels[i], LOW);
  }
  pinMode(UPPER_FLOAT, INPUT_PULLUP);
  pinMode(LOWER_FLOAT, INPUT_PULLUP);
  //pinMode(UPPER_FLOAT, INPUT);
  //pinMode(LOWER_FLOAT, INPUT);

  #if DEBUG || EEPROM_DEBUG
    Serial.begin(115200);

    strcpy_P(string_buffer, (char*)pgm_read_word(&(string_table[idx_initializing])));
    Serial.println(string_buffer);
  #endif

  byte macByte1 = EEPROM.read(0);

  #if DEBUG || EEPROM_DEBUG
    Serial.print("EEPROM.read(0): ");
    Serial.println(macByte1);
  #endif

  if(macByte1 == 255) {
	resetDefaults();
    if(Ethernet.begin(defaultMac) == 0) {
	  #if DEBUG
	    strcpy_P(string_buffer, (char*)pgm_read_word(&(string_table[idx_dhcp_failed])));
		Serial.println(string_buffer);
	  #endif
	  return;
	}
  }
  else {
    Ethernet.begin(mac, ip);
  }

  #if DEBUG || EEPROM_DEBUG
    Serial.print("MAC: ");
    for(int i=0; i<6; i++) {
      Serial.print(mac[i], HEX);
    }
    Serial.println();

    strcpy_P(string_buffer, (char*)pgm_read_word(&(string_table[idx_rest_address])));
    Serial.print(string_buffer);
    Serial.println(Ethernet.localIP());
  #endif

    httpServer.begin();
}

void loop() {

  handleActiveChannels();
  handleWebRequest();

  sensors.requestTemperatures();
  readResTemp();
  readTempHumidity();
  handleActiveChannels();
  handleWebRequest();

  readProbe(PH_ID, &PH);
  handleActiveChannels();
  handleWebRequest();

  readProbe(EC_ID, NULL);
  handleActiveChannels();
  handleWebRequest();

  readProbe(DO_ID, NULL);
  handleActiveChannels();
  handleWebRequest();

  readProbe(ORP_ID, &ORP);
  handleActiveChannels();
  handleWebRequest();
}

void readResTemp() {
  debug("Reading OneWire temperatures");
  resTemp = sensors.getTempFByIndex(0);

  if(DEBUG) {
    Serial.print("Res Temp: ");
    Serial.println(resTemp);
  }
}

float zeroIfNan(float number) {
  if(isnan(number)) {
	number = 0.0;
  }
  return number;
}

void readTempHumidity() {

  debug("Reading environment temp, humidity, & heat index");
  envTemp = zeroIfNan(envDHT.readTemperature(true));
  envHumidity = zeroIfNan(envDHT.readHumidity());
  envHeatIndex = zeroIfNan(envDHT.computeHeatIndex(envTemp, envHumidity));

  if(DEBUG) {
    Serial.print("Environment Temp: ");
    Serial.println(envTemp);
    Serial.print("Environment Humidity: ");
    Serial.println(envHumidity);
    Serial.print("Environment Heat Index: ");
    Serial.println(envHeatIndex);
  }
}

void readProbe(int channel, float *probe) {

  debug("Reading ISE probes");

  Wire.beginTransmission(channel);
  Wire.write('r');
  Wire.endTransmission();
  delay(1000);

  char sensordata[30];
  byte sensor_bytes_received = 0;
  byte code = 0;
  byte in_char = 0;

  sensor_bytes_received = 0;
  memset(sensordata, 0, sizeof(sensordata));

  Wire.requestFrom(channel, 48, 1);
  code = Wire.read();

  while(Wire.available()) {

    in_char = Wire.read();
    if (in_char == 0) {
      Wire.endTransmission();
      break;
    }
    else {
      sensordata[sensor_bytes_received] = in_char;
      sensor_bytes_received++;
    }
  }

  if(DEBUG) {
    switch (code) {                       // switch case based on what the response code is.
      case 1:                             // decimal 1  means the command was successful.
      Serial.println(sensordata);         // print the actual reading
      break;                              // exits the switch case.

      case 2:                             // decimal 2 means the command has failed.
      Serial.println("command failed");   // print the error
      break;                              // exits the switch case.

      case 254:                           // decimal 254  means the command has not yet been finished calculating.
      Serial.println("circuit not ready"); // print the error
      break;                              // exits the switch case.

      case 255:                           // decimal 255 means there is no further data to send.
      Serial.println("no data");          // print the error
      break;                              // exits the switch case.
    }
    Serial.print("[Sensordata] Channel: ");
    Serial.print(channel);
    Serial.print(", value: ");
    Serial.println(sensordata);
  }

  char * pch;

  if(channel == EC_ID) {
    pch = strtok(sensordata, ",");
    EC = atof(pch);
    TDS = atof(strtok(NULL, ","));
    SAL = atof(strtok(NULL, ","));
    SG = atof(strtok(NULL, ","));
    if(DEBUG) {
      Serial.print("EC: ");
      Serial.println(EC);
      Serial.print("TDS: ");
      Serial.println(TDS);
      Serial.print("SAL: ");
      Serial.println(SAL);
      Serial.print("SG: ");
      Serial.println(SG);
    }
    return;
  }
  else if (channel == DO_ID) {
    pch = strtok(sensordata, ",");
    DO_mgL = atof(pch);
    DO_PER = atof(strtok(NULL, ","));
    if(DEBUG) {
      Serial.print("DO mg/L: ");
      Serial.println(DO_mgL);
      Serial.print("DO Percent: ");
      Serial.println(DO_PER);
    }
    return;
  }
  else {
    *probe = atof(sensordata);
  }
}

void switchOn(int pin) {
#if DEBUG
  char sPin[3];
  itoa(pin, sPin, 10);
  strcpy_P(string_buffer, (char*)pgm_read_word(&(string_table[idx_switch_on])));
  strcat(string_buffer, " pin ");
  strcat(string_buffer, sPin);
  Serial.println(string_buffer);
#endif
  digitalWrite(pin, HIGH);
}

void switchOff(int pin) {
#if DEBUG
  char sPin[3];
  itoa(pin, sPin, 10);
  strcpy_P(string_buffer, (char*)pgm_read_word(&(string_table[idx_switch_off])));
  strcat(string_buffer, " pin ");
  strcat(string_buffer, sPin);
  Serial.println(string_buffer);
#endif
  digitalWrite(pin, LOW);
}

void debug(String msg) {
  if(DEBUG) {
    Serial.println(msg);
  }
}

void handleActiveChannels() {
	unsigned long currentMillis = millis();

	for(int i=0; i<CHANNEL_SIZE; i++) {
		if(channel_table[i][0] != NULL_CHANNEL) {
			if(currentMillis - channel_table[i][1] > channel_table[i][2]) {

				digitalWrite(channel_table[i][0], LOW);

				#if DEBUG
				  Serial.print("Turning channel ");
				  Serial.print(i);
				  Serial.print(" (pin ");
				  Serial.print(channel_table[i][0]);
				  Serial.print(") off after ");
				  Serial.print(channel_table[i][2] / 1000);
				  Serial.println(" seconds");
				#endif

				channel_table[i][0] = NULL_CHANNEL;
				channel_table[i][1] = 0;
				channel_table[i][2] = 0;
			}
		}
	}
}

void handleWebRequest() {

	httpClient = httpServer.available();

	char clientline[BUFSIZE] = {0};
	int index = 0;

	bool reboot = false;
	char json[500];
	char sPin[3];
	char state[3];

	if (httpClient) {

		// reset input buffer
		index = 0;

		while (httpClient.connected()) {

			if (httpClient.available()) {

				char c = httpClient.read();
				if (c != '\n' && c != '\r' && index < BUFSIZE) {
					clientline[index++] = c;
					continue;
				}

				httpClient.flush();

				String urlString = String(clientline);
				String op = urlString.substring(0, urlString.indexOf(' '));
				urlString = urlString.substring(urlString.indexOf('/'), urlString.indexOf(' ', urlString.indexOf('/')));
				urlString.toCharArray(clientline, BUFSIZE);

				char *resource = strtok(clientline, "/");
				char *param1 = strtok(NULL, "/");
				char *param2 = strtok(NULL, "/");

				#if DEBUG
				  Serial.print("Resource: ");
				  Serial.println(resource);

				  Serial.print("Parm1: ");
				  Serial.println(param1);

				  Serial.print("Param2: ");
				  Serial.println(param2);
				#endif

				// /state
				if (strncmp(resource, "state", 5) == 0) {

					strcpy(json, json_bracket_open);

					  strcpy_P(string_buffer, (char*)pgm_read_word(&(string_table[idx_json_key_metrics])));
					  strcat(json, string_buffer);

					    strcpy_P(string_buffer, (char*)pgm_read_word(&(string_table[idx_json_key_mem])));
					    strcat(json, string_buffer);
					    itoa(availableMemory(), float_buffer, 10);
					    strcat(json, float_buffer);

					    strcpy_P(string_buffer, (char*)pgm_read_word(&(string_table[idx_json_key_envTemp])));
					    strcat(json, string_buffer);
					    dtostrf(envTemp, 4, 2, float_buffer);
					    strcat(json, float_buffer);

					    strcpy_P(string_buffer, (char*)pgm_read_word(&(string_table[idx_json_key_envHumidity])));
					    strcat(json, string_buffer);
					    dtostrf(envHumidity, 4, 2, float_buffer);
					    strcat(json, float_buffer);

					    strcpy_P(string_buffer, (char*)pgm_read_word(&(string_table[idx_json_key_envHeatIndex])));
					    strcat(json, string_buffer);
                      	dtostrf(envHeatIndex, 4, 2, float_buffer);
                      	strcat(json, float_buffer);

                      	strcpy_P(string_buffer, (char*)pgm_read_word(&(string_table[idx_json_key_ph])));
                      	strcat(json, string_buffer);
                      	dtostrf(PH, 4, 2, float_buffer);
                      	strcat(json, float_buffer);

                      	strcpy_P(string_buffer, (char*)pgm_read_word(&(string_table[idx_json_key_ec])));
                      	strcat(json, string_buffer);
                      	dtostrf(EC, 4, 2, float_buffer);
                      	strcat(json, float_buffer);

                      	strcpy_P(string_buffer, (char*)pgm_read_word(&(string_table[idx_json_key_tds])));
                      	strcat(json, string_buffer);
                      	dtostrf(TDS, 4, 2, float_buffer);
                      	strcat(json, float_buffer);

                      	strcpy_P(string_buffer, (char*)pgm_read_word(&(string_table[idx_json_key_sal])));
                      	strcat(json, string_buffer);
                      	dtostrf(SAL, 4, 2, float_buffer);
                      	strcat(json, float_buffer);

                      	strcpy_P(string_buffer, (char*)pgm_read_word(&(string_table[idx_json_key_sg])));
                      	strcat(json, string_buffer);
                      	dtostrf(SG, 4, 2, float_buffer);
                      	strcat(json, float_buffer);

                      	strcpy_P(string_buffer, (char*)pgm_read_word(&(string_table[idx_json_key_do_mgl])));
                      	strcat(json, string_buffer);
                      	itoa(DO_mgL, float_buffer, 10);
                      	strcat(json, float_buffer);

                      	strcpy_P(string_buffer, (char*)pgm_read_word(&(string_table[idx_json_key_do_per])));
                      	strcat(json, string_buffer);
                      	itoa(DO_PER, float_buffer, 10);
                      	strcat(json, float_buffer);

                      	strcpy_P(string_buffer, (char*)pgm_read_word(&(string_table[idx_json_key_orp])));
                      	strcat(json, string_buffer);
                      	itoa(ORP, float_buffer, 10);
                      	strcat(json, float_buffer);

                      	strcpy_P(string_buffer, (char*)pgm_read_word(&(string_table[idx_json_key_resTemp])));
                      	strcat(json, string_buffer);
                      	dtostrf(resTemp, 4, 2, float_buffer);
                      	strcat(json, float_buffer);

                      	strcpy_P(string_buffer, (char*)pgm_read_word(&(string_table[idx_json_key_upperFloat])));
                      	strcat(json, string_buffer);
                      	dtostrf(analogRead(UPPER_FLOAT), 4, 2, float_buffer);
                      	strcat(json, float_buffer);

                      	strcpy_P(string_buffer, (char*)pgm_read_word(&(string_table[idx_json_key_lowerFloat])));
                      	strcat(json, string_buffer);
                      	dtostrf(analogRead(LOWER_FLOAT), 4, 2, float_buffer);
                      	strcat(json, float_buffer);

					  strcat(json, json_bracket_close);

                      strcpy_P(string_buffer, (char*)pgm_read_word(&(string_table[idx_json_key_channels])));
                      strcat(json, string_buffer);
						for(int i=0; i<CHANNEL_SIZE; i++) {
						  itoa(digitalRead(channels[i]), state, 10);
						  strcat(json, state);
						  if(i + 1 < CHANNEL_SIZE) {
						    strcat(json, ",");
						  }
						}
					  strcat(json, json_array_bracket_close);

					strcat(json, json_bracket_close);
				}

				// /eeprom
				else if (strncmp(resource, "eeprom", 6) == 0) {
					#if EEPROM_DEBUG
						Serial.println("/eeprom");
						Serial.println(param1);
						Serial.println(param2);
					#endif

					EEPROM.write(atoi(param1), atoi(param2));

					strcpy(json, json_bracket_open);

					  strcpy_P(string_buffer, (char*)pgm_read_word(&(string_table[idx_json_key_address])));
					  strcat(json, string_buffer);
					  strcat(json, param1);

					  strcpy_P(string_buffer, (char*)pgm_read_word(&(string_table[idx_json_key_value])));
					  strcat(json, string_buffer);
					  strcat(json, param2);

					strcat(json, json_bracket_close);
				}

				// /timer/{channel}/{seconds}
				else if (strncmp(resource, "timer", 5) == 0) {

					if(param1 == NULL || param1 == "") {
						Serial.println("parameter required");
						//send500("parameter required");
						break;
					}

					int channel = atoi(param1);
					unsigned long duration = strtoul(param2, NULL, 10);

					if(channel >= 0 && channel < CHANNEL_SIZE && duration > 0) {

						#if DEBUG
						  Serial.print("Channel: ");
						  Serial.println(channel);

						  Serial.print("Duration: ");
						  Serial.println(duration);
						#endif

						channel_table[channel][0] = channels[channel];
						channel_table[channel][1] = millis();
						channel_table[channel][2] = duration * 1000;

						digitalWrite(channels[channel], HIGH);
					}
					else {
					  #if DEBUG
						Serial.println("Invalid channel/duration");
					  #endif
					}

					strcpy(json, "{");

						strcat(json, "\"channel\":");
						itoa(channel, float_buffer, 10);
						strcat(json, float_buffer);

						strcat(json, ",\"duration\":");
						itoa(duration, float_buffer, 10);
						strcat(json, float_buffer);

					strcat(json, "}");
				}

				// /switch/{channel}/{position}     1 = on, else off
				else if (strncmp(resource, "switch", 6) == 0) {

					bool valid = false;
					int channel = atoi(param1);
					int position = atoi(param2);

					if(channel >= 0 && channel < CHANNEL_SIZE) {
						valid = true;
					}

					if(valid) {

						position == 1 ? switchOn(channels[channel]) : switchOff(channels[channel]);

						strcpy(json, json_bracket_open);

						  strcpy_P(string_buffer, (char*)pgm_read_word(&(string_table[idx_json_key_channel])));
						  strcat(json, string_buffer);
						  strcat(json, param1);

						  strcpy_P(string_buffer, (char*)pgm_read_word(&(string_table[idx_json_key_pin])));
						  strcat(json, string_buffer);
						  itoa(channels[channel], string_buffer, 10);
						  strcat(json, string_buffer);
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

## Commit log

2019-03-06 add initial ro solenoid logic
2019-04-03 remove aREST. add /reset, /reboot, /eeprom, /status endpoints
    [main.cpp]
2019-04-03 fix json formatting bug
    [main.cpp]
2019-04-06 reset mac address to default. make string_buffer larger
    [main.cpp]
2019-04-29 add /switch and /dispense endpoints
2019-05-07 add upper and lower float valve. refactor switch to include channel and pin
2019-05-08 fix switch channel / pin json formatting
    [main.cpp]
2019-06-12 add call to resetDefaults if macByte1 is 255
    [main.cpp]
2020-02-03 add kicad project
    [cropdroid-reservoir-B_Cu.gbl, cropdroid-reservoir-B_Cu.gbr, cropdroid-reservoir-B_Mask.gbr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]
2020-02-04 refactor kicad folder to hardware
    [cropdroid-reservoir-B_Cu.gbl, cropdroid-reservoir-B_Cu.gbr, cropdroid-reservoir-B_Mask.gbr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]
2020-02-05 complete prototype v0.1a
    [cropdroid-reservoir-B_Cu.gbl, cropdroid-reservoir-B_Cu.gbr, cropdroid-reservoir-B_Mask.gbr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]
2020-02-05 move logo to libraries folder
    [cropdroid-reservoir.kicad_pcb, cropdroid-reservoir.sch]
2020-02-09 add cropdroid-reservoir-120v design
    [cropdroid-reservoir-B_Cu.gbl, cropdroid-reservoir-B_Mask.gbs, cropdroid-reservoir-B_Paste.gbp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]
2020-02-09 clean up kicad libs
    [cropdroid-reservoir-B_Cu.gbl, cropdroid-reservoir-B_Mask.gbs, cropdroid-reservoir-B_Paste.gbp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]
2020-02-10 final kicad v0.2a
    [bom.csv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]
2020-02-10 final v0.3a iterations
    [cropdroid-reservoir.kicad_pcb]
2020-02-21 add v0.5a hardware
    [bom.csv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]
2020-02-21 v0.5a final
    [cropdroid-reservoir-B_Cu.gbl, cropdroid-reservoir-B_Mask.gbs, cropdroid-reservoir-B_Paste.gbp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]
2020-02-21 remove xml bom
    [cropdroid-reservoir.kicad_pcb]
2020-03-01 v0.6a hardware
    [bom.csv, cropdroid-reservoir.kicad_pcb, cropdroid-reservoir.sch]
2020-03-01 fix broken board edge
    [cropdroid-reservoir-B_Cu.dxf, cropdroid-reservoir-B_Mask.dxf, cropdroid-reservoir-B_Paste.dxf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]
2020-03-01 add board dimension drawings. space dc power jacks 3/4 in apart
    [cropdroid-reservoir-B_Cu.dxf, cropdroid-reservoir-B_Mask.dxf, cropdroid-reservoir-F_Cu.dxf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]
2020-03-02 rename gerber folder to plots, generate final v0.6a artifacts for fab shop
    [cropdroid-reservoir-B_Cu.dxf, cropdroid-reservoir-B_Mask.dxf, cropdroid-reservoir-B_Paste.dxf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]
2020-03-11 add /sys endpoint
    [cropdroid-reservoir.kicad_pcb, cropdroid-reservoir.sch]
2020-04-13 return metrics as array. fix /reboot and /reset, rename /dispense to /timer
    [cropdroid-reservoir-B_Cu.dxf, cropdroid-reservoir-B_Mask.dxf, cropdroid-reservoir-B_Paste.dxf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]
2021-07-27 move float pins to A14 and A15 to avoid conflict w/ ethernet. fix memory leak and channel size bug
    [main.cpp]
2024-01-16 Add hardware flow image

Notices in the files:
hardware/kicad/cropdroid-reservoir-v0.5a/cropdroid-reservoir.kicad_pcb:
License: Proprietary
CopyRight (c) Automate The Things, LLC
